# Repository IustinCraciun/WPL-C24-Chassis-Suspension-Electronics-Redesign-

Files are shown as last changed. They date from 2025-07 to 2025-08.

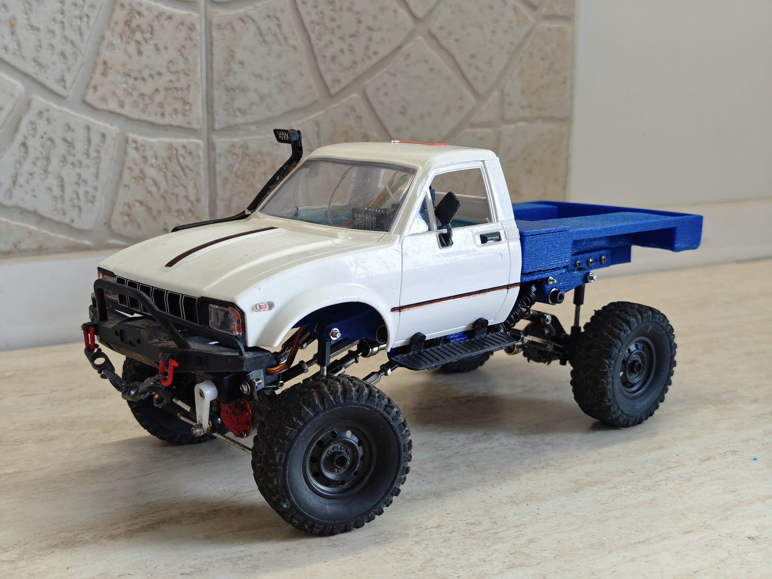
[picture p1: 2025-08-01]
photos/Fully_assembled.jpeg

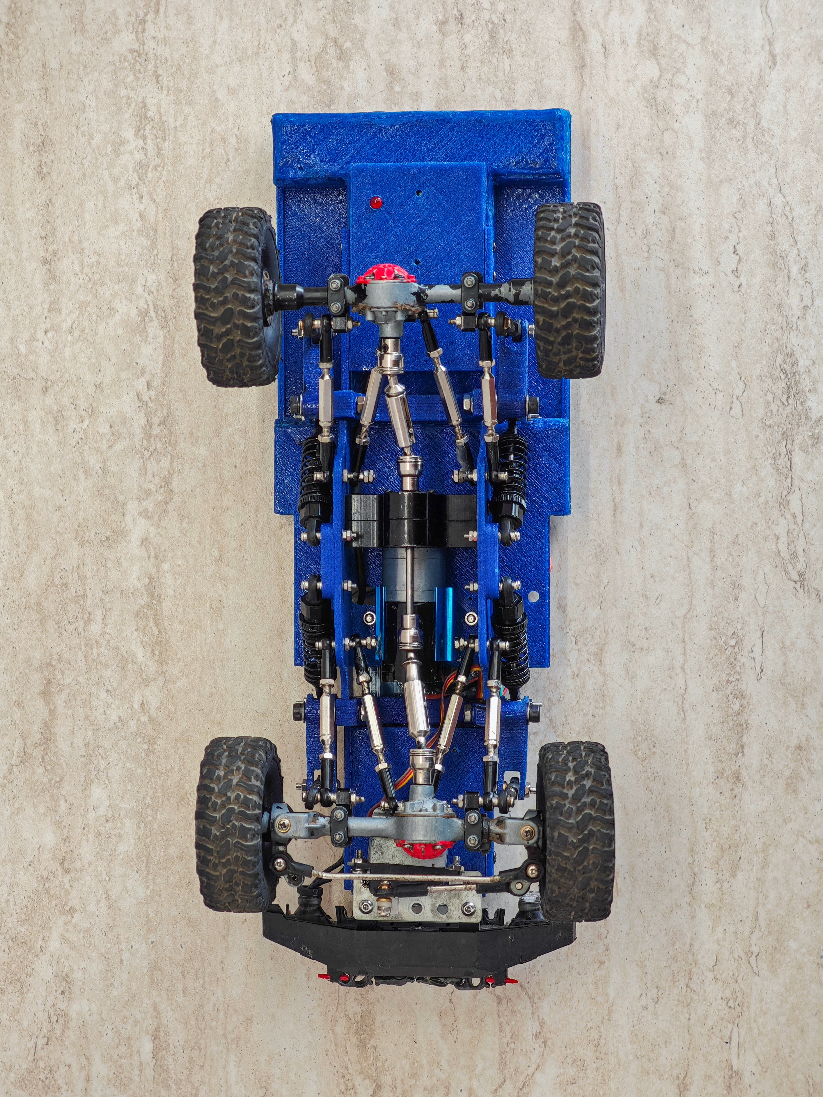
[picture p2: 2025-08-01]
photos/Underneath_view.jpeg

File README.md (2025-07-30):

This project started as a complete redesign of a WPL C24 remote-controlled car. I designed a custom chassis featuring a cantilever (push-rod) suspension system to significantly improve its off-road capabilities. The electronics were changed entirely(except for the servomotor):
An Arduino Pro Micro as the main controller
An RC receiver for input signals
A BTS7960 motor driver for high-current motor control
A 7.4V / 3400mAh Li-ion battery pack for extended runtime
A LM2596 DC to DC converter, for powering the Arduino Pro Micro with stabilized 5V

I also upgraded the drivetrain by installing a high-torque motor with a metal gearbox for better performance and durability. The only original part remaining from the WPL C24 is the cab.

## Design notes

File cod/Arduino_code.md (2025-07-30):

#include <Servo.h>

//rc receptor pins 
#define CH1_pin 18
#define CH2_pin 19
#define CH3_pin 20
#define CH4_pin 21

//BTS7960 driver pins
const int motorRPWM = 5;
const int motorLPWM = 6;
const int motorEN1 = 7;
const int motorEN2 = 8;

//led pin
const int LED_pin = 10;

//Servo object
Servo myServo;
int neutralServoAngle = 90; //setting neutral angle
int servoAngle;

//variables for motor control
int intermediarMotorSpeed = 0;
int motorSpeed = 0;
bool motorDirection = true;

//variables for pwm signal stabilization
float alpha = 0.3; //smoothness coeficient !!change this for smoother or sharper signal variations!!
//variables for filtered values
float filteredCH1 = 0;
float filteredCH2 = 0;

//exponential smoothness function
int applyExponentialFilter(float &filteredValue, int rawValue) {
  filteredValue = alpha * rawValue + (1-alpha) * filteredValue;
  return (int)filteredValue;
}

void setup() {

  // rc receptor pins configuration
  pinMode(CH1_pin, INPUT);
  pinMode(CH2_pin, INPUT);
  pinMode(CH3_pin, INPUT);
  pinMode(CH4_pin, INPUT);

  //output pins for BTS7960
  pinMode(motorLPWM, OUTPUT);
  pinMode(motorRPWM, OUTPUT);
  pinMode(motorEN1, OUTPUT);
  pinMode(motorEN2, OUTPUT);

  //led pin
  pinMode(LED_pin, OUTPUT);

  //servo pin
  myServo.attach(3);

  //serial initialization for debugging
  //Serial.begin(9600);

}

void loop() {
  
  //extracting signals from the receptor
  int rawpwmCH1 = pulseIn(CH1_pin, HIGH, 25000);
  int rawpwmCH2 = pulseIn(CH2_pin, HIGH, 25000);
  int pwmCH3 = pulseIn(CH3_pin, HIGH, 25000);
  int pwmCH4 = pulseIn(CH4_pin, HIGH, 25000);

  int pwmCH1 = applyExponentialFilter(filteredCH1, rawpwmCH1);
  int pwmCH2 = applyExponentialFilter(filteredCH2, rawpwmCH2);
  //debugging
  //Serial.println(LED_pin);

  //control servo (CH1)
  if(pwmCH1 >= 930 && pwmCH1 <= 2070) {
    servoAngle = map(pwmCH1, 930, 2070, -40, 40);
    int servoPosition = neutralServoAngle + servoAngle;
    myServo.write(servoPosition);
  }

  //control motor (CH2)
  if(pwmCH2 >=900 && pwmCH2 <= 2130) {
    if(pwmCH2 > 1560) {
      motorDirection = true; //forward
      if(pwmCH2 <=2070) {
       intermediarMotorSpeed = map(pwmCH2, 1560, 2070, 0, 255 ); 
      } else if(pwmCH2 > 2070){
        intermediarMotorSpeed = 255;
      }
      
    } else if (pwmCH2 < 1520) {
      motorDirection = false; //backward
      if(pwmCH2 >= 950){
        intermediarMotorSpeed = map(pwmCH2, 950, 1520, 255, 0);
      } else if (pwmCH2 < 950) {
        intermediarMotorSpeed = 255;
      }
      
    } else {
      intermediarMotorSpeed = 0; //stop
    }
    
    //speed controll
    if(pwmCH3 < 1500){
      motorSpeed = intermediarMotorSpeed / 2;
    } else if(pwmCH3 > 1500){
      motorSpeed = intermediarMotorSpeed;
    }

    controlMotor(motorSpeed, motorDirection);

  } else {
    controlMotor(0, true); // invalid signal-> motor stop
  }
  
  //control led (CH4)
  if(pwmCH4 > 1500) {
    digitalWrite(LED_pin, HIGH);
  } else if (pwmCH4 < 1500) {
    digitalWrite(LED_pin, LOW);
  }
  
  delay(10); //delay for stabilization
}

//function for controlling the motor 
void controlMotor(int speed, bool direction) {
  if (direction) { // forward
    analogWrite(motorRPWM, speed); 
    analogWrite(motorLPWM, 0);   
    digitalWrite(motorEN1, HIGH); 
    digitalWrite(motorEN2, HIGH);  
  } else if(!direction){ // reverse
    analogWrite(motorRPWM, 0);    
    analogWrite(motorLPWM, speed); 
    digitalWrite(motorEN1, HIGH);  
    digitalWrite(motorEN2, HIGH); 
  } else {
    analogWrite(motorRPWM, 0);
    analogWrite(motorLPWM, 0);
    digitalWrite(motorEN1, LOW);
    digitalWrite(motorEN2, LOW);
  }
}

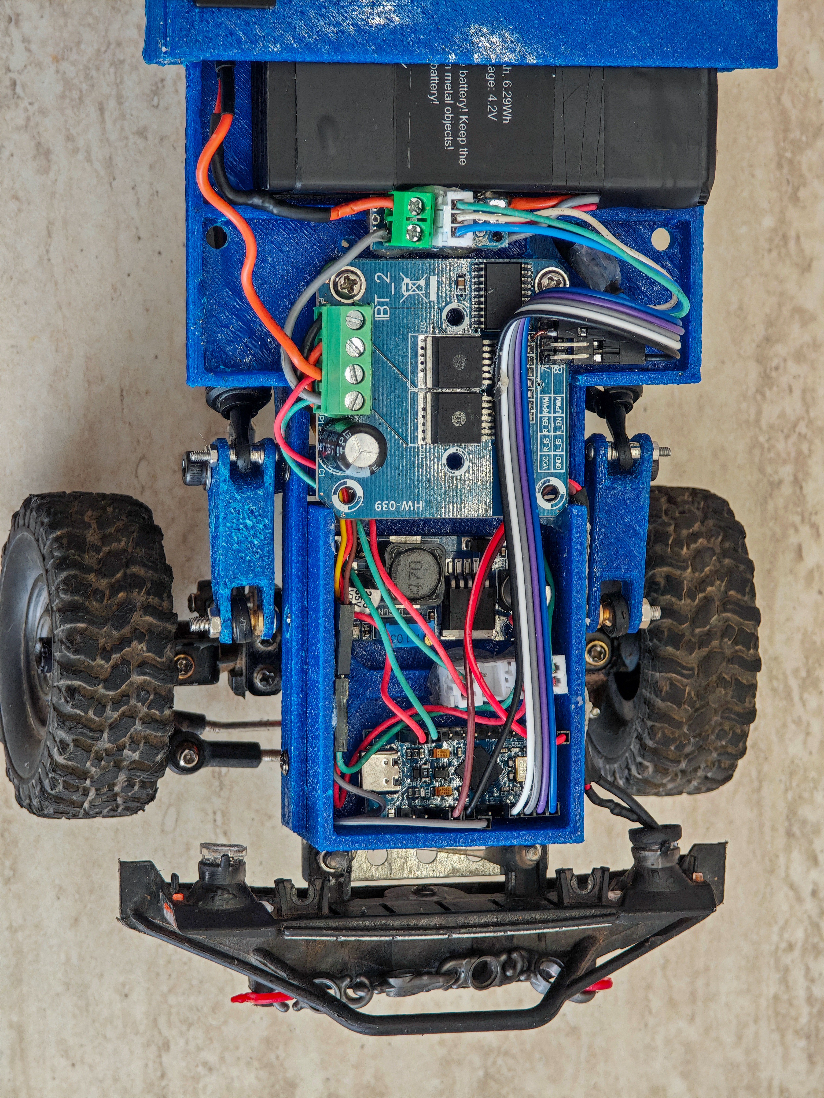
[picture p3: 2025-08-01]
photos/Circuits_tray.jpeg

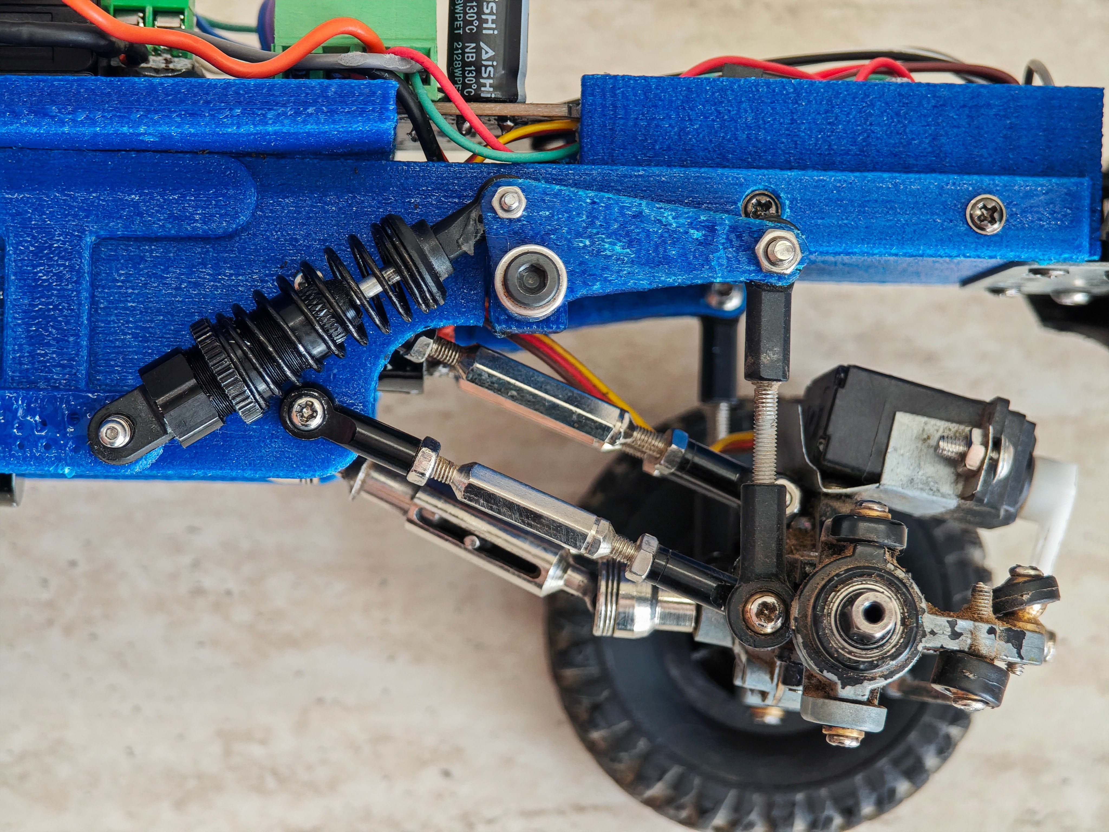
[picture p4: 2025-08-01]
photos/Front_suspension.jpeg

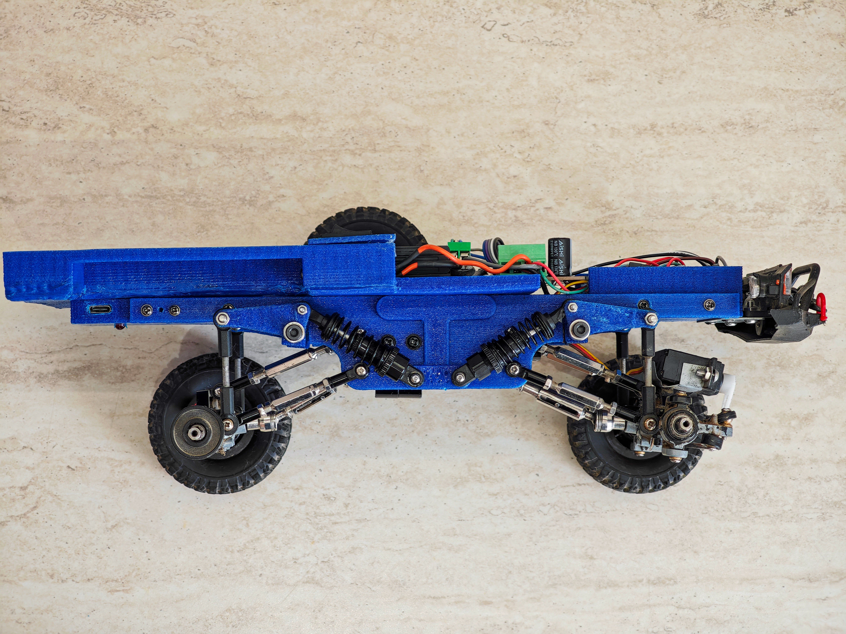
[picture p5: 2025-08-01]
photos/Side_view.jpeg

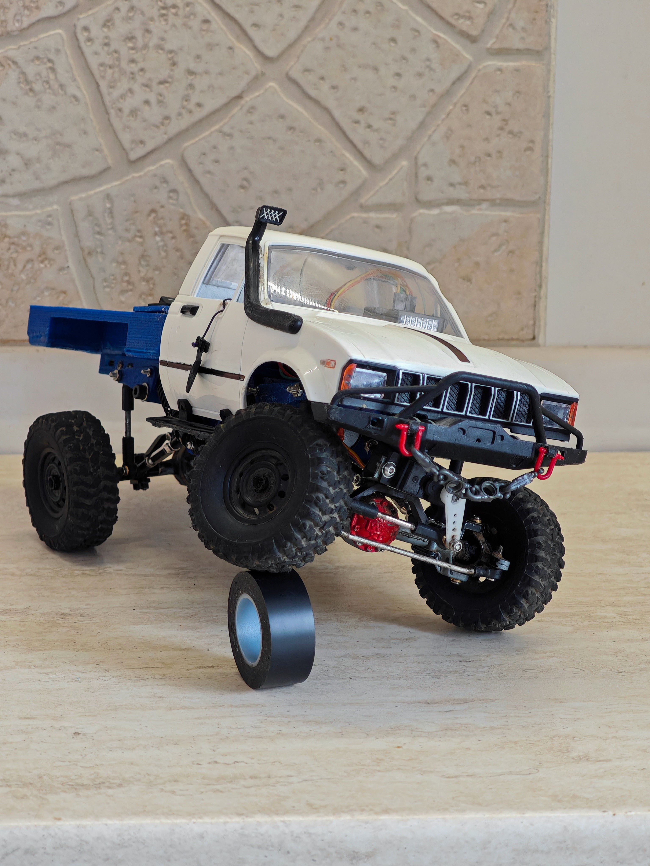
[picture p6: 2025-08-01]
photos/Suspension_travel.jpeg

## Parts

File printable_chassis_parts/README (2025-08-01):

Here are all the parts necesary for the whole chassis.
Also, if you have SolidWorks, you can open the Chassis assembly to see how to assemble all the parts

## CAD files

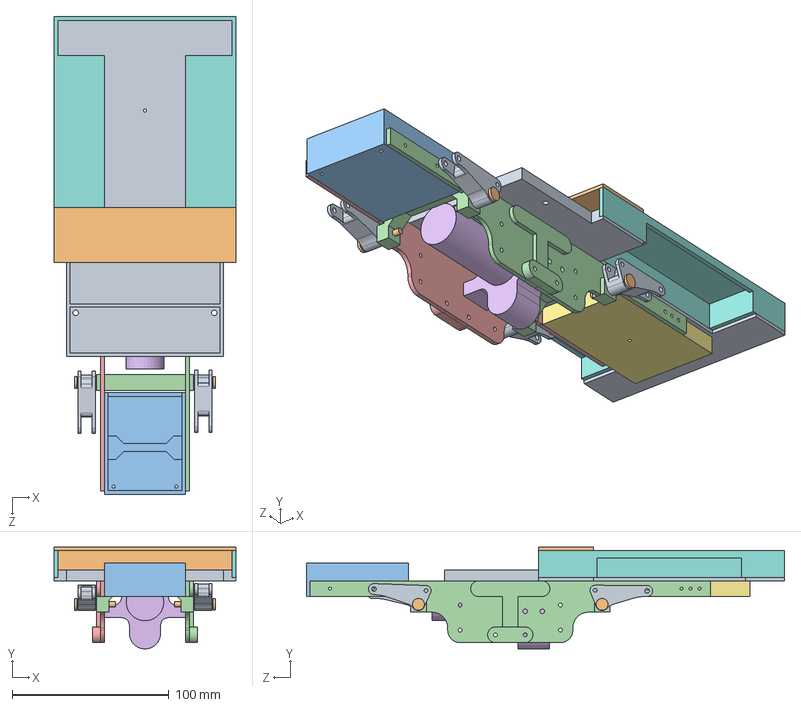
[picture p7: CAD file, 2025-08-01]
printable_chassis_parts/Chassis.SLDASM
116.0 x 64.9 x 305.3 mm
Oscilating_arm x 4
suspension_pin x 4
M4_washer x 8
Suspension_Mounting x 2
Right_Chassis_frame
Motor_Assembly
Rear_tray
bed_side_walls
bed_base_2
Battery_tray_top
Front_box
Left_Chassis_frame

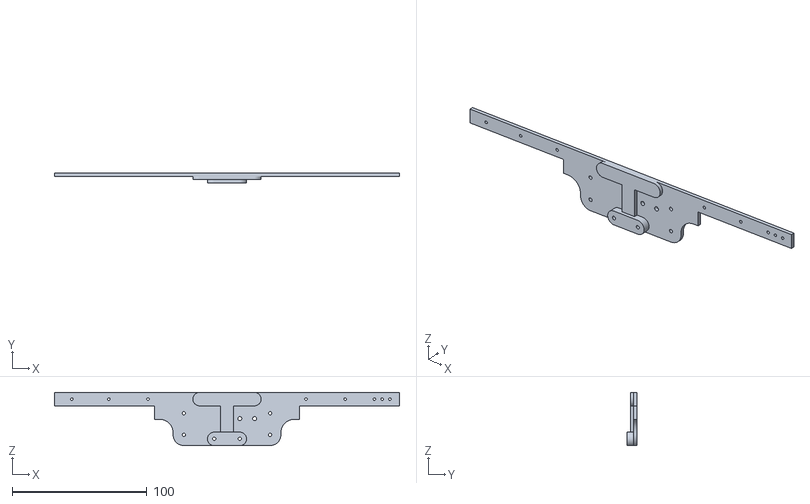
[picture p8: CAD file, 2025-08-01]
printable_chassis_parts/Left_Chassis_frame_print.STL
256.0 x 7.50 x 39.5

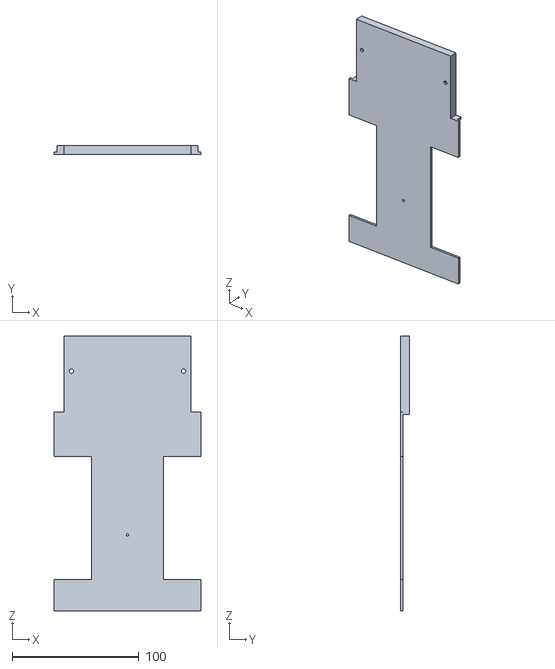
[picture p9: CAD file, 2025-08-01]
printable_chassis_parts/bed_base_2_print.STL
116.0 x 7.00 x 217.1

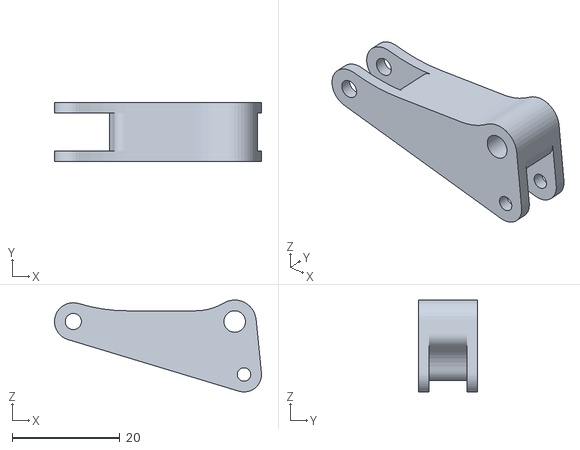
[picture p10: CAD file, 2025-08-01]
printable_chassis_parts/Oscilating_arm_print.STL
38.5 x 11.0 x 17.1

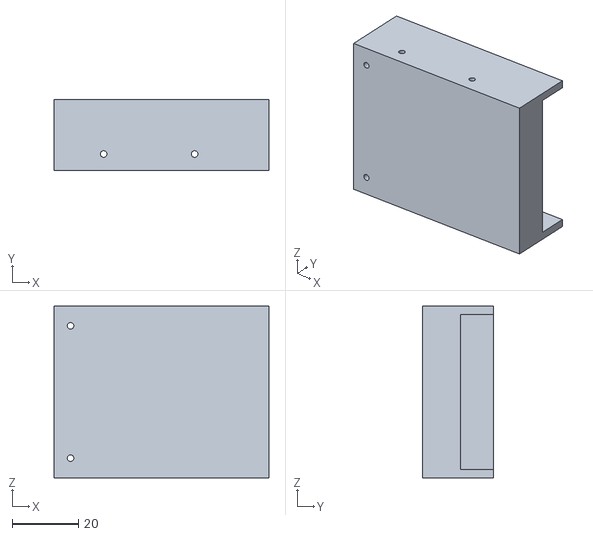
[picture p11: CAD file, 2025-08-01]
printable_chassis_parts/Front_box_print.STL
65.0 x 21.5 x 52.0

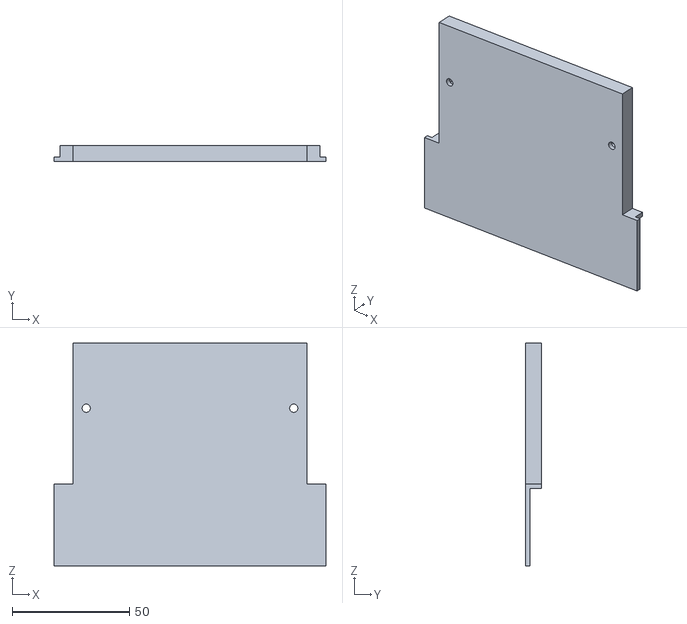
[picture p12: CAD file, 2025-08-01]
printable_chassis_parts/Battery_tray_print.STL
116.0 x 7.00 x 95.0

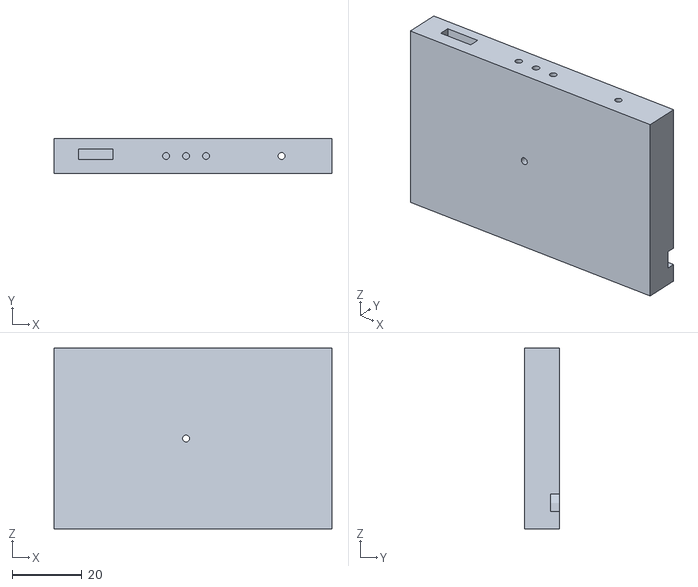
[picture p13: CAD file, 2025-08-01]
printable_chassis_parts/Rear_tray_print.STL
80.0 x 10.0 x 52.0

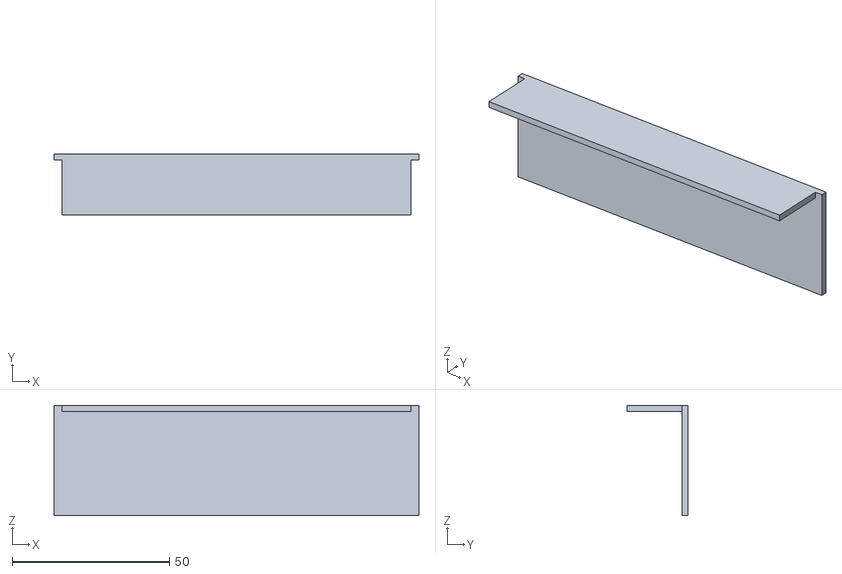
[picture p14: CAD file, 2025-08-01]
printable_chassis_parts/Battery_tray_top_print.STL
116.0 x 19.5 x 35.0

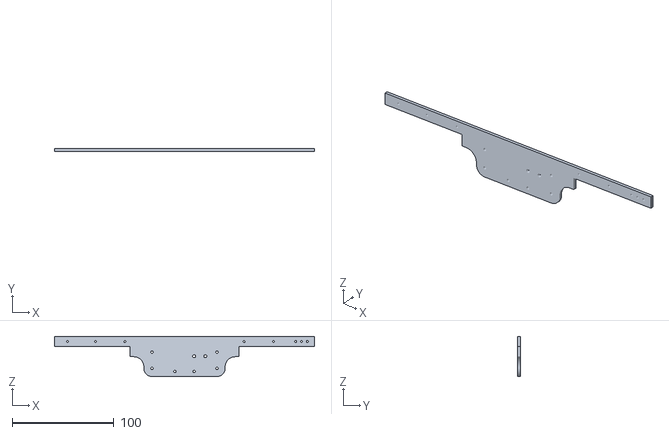
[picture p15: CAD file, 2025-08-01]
printable_chassis_parts/Chassis_frame_print.STL
256.0 x 2.50 x 39.5

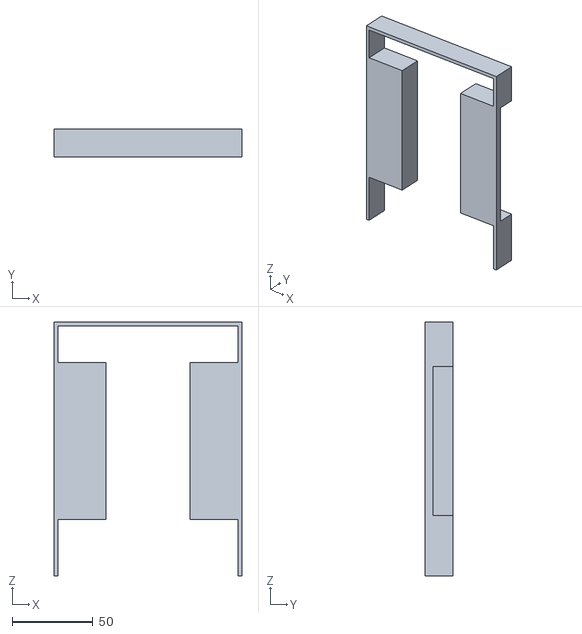
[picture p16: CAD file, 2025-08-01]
printable_chassis_parts/bed_side_walls_print.STL
116.0 x 17.5 x 157.1

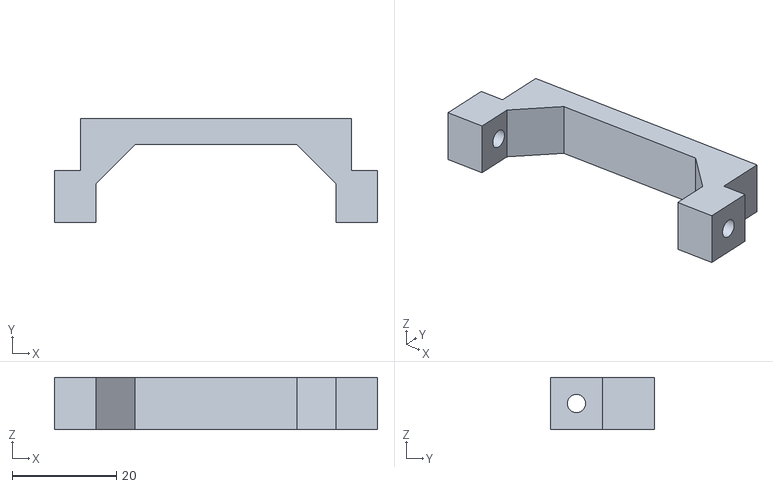
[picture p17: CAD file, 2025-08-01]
printable_chassis_parts/Suspension_Mounting_print.STL
62.0 x 20.0 x 10.0

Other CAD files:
printable_chassis_parts/Right_Chassis_frame_print.STL
